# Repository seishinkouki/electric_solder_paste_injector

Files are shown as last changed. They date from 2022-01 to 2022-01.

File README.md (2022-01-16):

# electric_solder_paste_injector
## 电动锡膏注射器说明
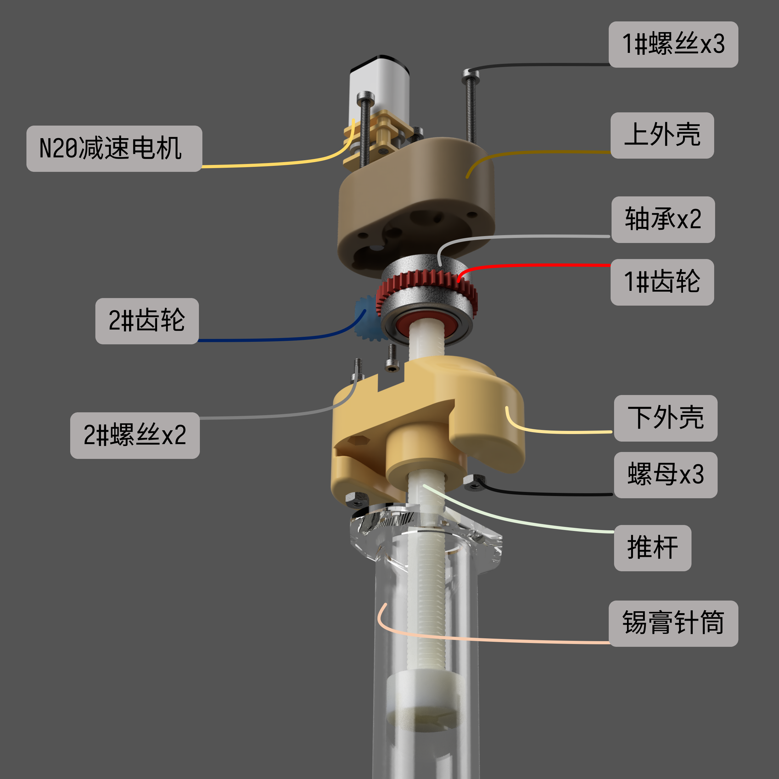
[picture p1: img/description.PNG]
图片

1. N20 减速电机: 5v电压, 150转左右均可, 出轴为10mm长, 直径3mm D轴, [淘宝链接](https://item.taobao.com/item.htm?id=592127519086)
2. 1#螺丝: m2x25mm, 淘宝购买
3. 2#螺丝: m1.6x4mm, 淘宝购买
4. 螺母: m2, 淘宝购买
5. 轴承: 内径12 外径18 厚4mm, 型号6701ZZ, [淘宝链接](https://detail.tmall.com/item.htm?id=585453925523&skuId=3967291013296)
6. 上外壳: 3d打印
7. 下外壳: 3d打印
8. 1#齿轮: 0.5模38齿, 3d打印
9. 2#齿轮: 0.5模15齿, 3mm D轴, [淘宝链接](https://item.taobao.com/item.htm?id=624015580884)
10. 推杆: 3d打印
11. 钢珠x6: 直径2mm, [淘宝链接](https://detail.tmall.com/item.htm?id=624796630554&skuId=4595617071063)
12. 锡膏针筒: 商品锡膏针筒
# 备注: 3d打印需使用尼龙材料才能达到强度要求, 已验证未来工场"尼龙加纤"材料, 其它尼龙材料理论也可行

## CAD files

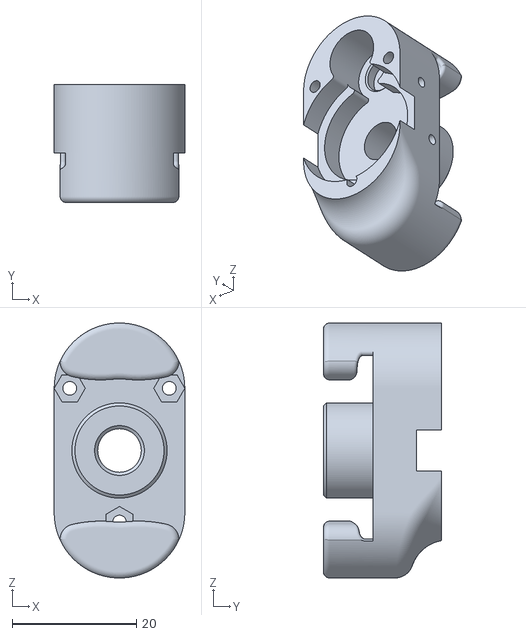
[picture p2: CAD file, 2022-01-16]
3d_model/下外壳.stl
21.0 x 19.0 x 41.0

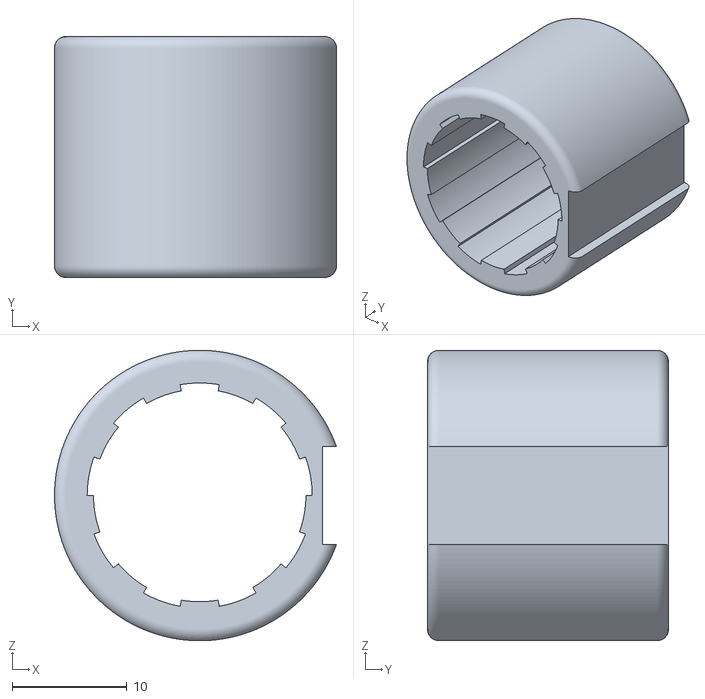
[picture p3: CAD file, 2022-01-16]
3d_model/控制.stl
24.6 x 21.0 x 25.3

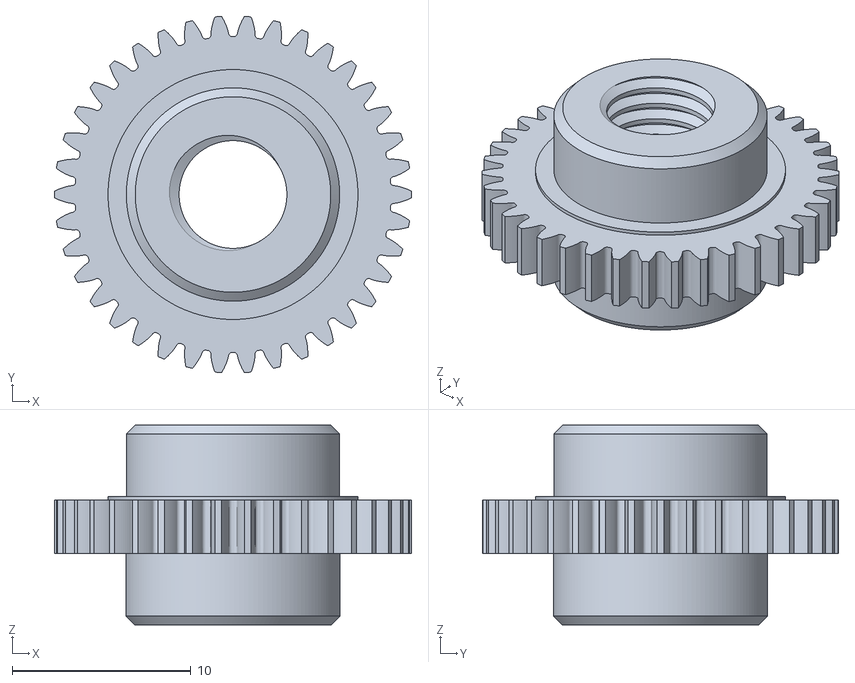
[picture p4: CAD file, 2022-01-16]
3d_model/齿轮.stl
20.0 x 20.0 x 11.2

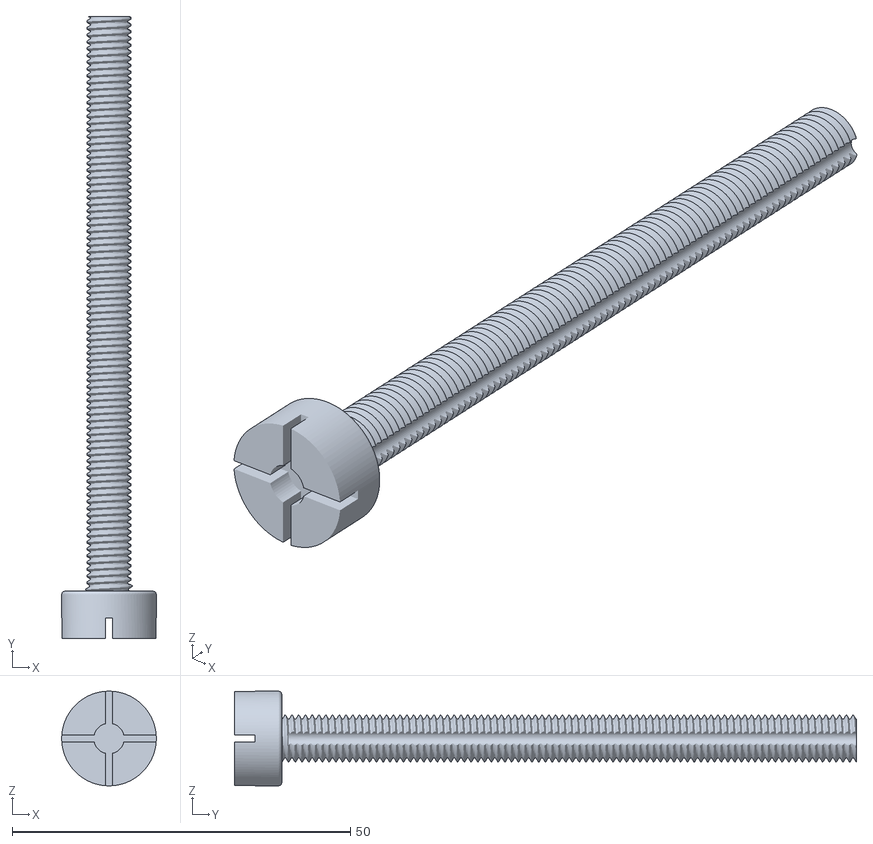
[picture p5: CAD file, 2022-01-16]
3d_model/推杆.stl
14.0 x 92.0 x 14.0

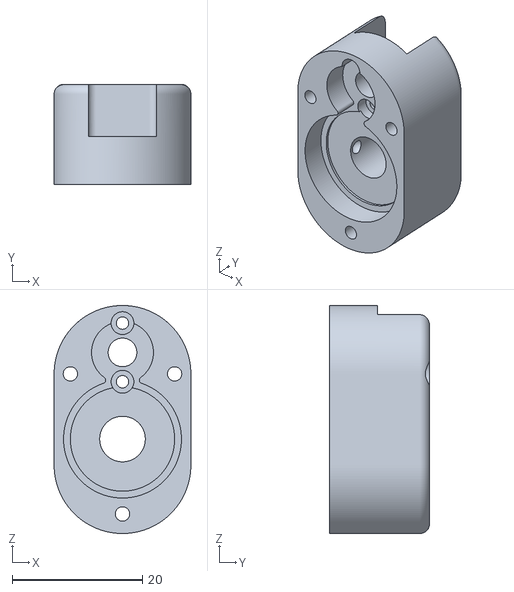
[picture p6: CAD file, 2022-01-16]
3d_model/上外壳.stl
21.0 x 15.4 x 35.0

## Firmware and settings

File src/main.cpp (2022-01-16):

#include <Arduino.h>
#include <AsyncTCP.h>
#include <Preferences.h>
#include <ESPAsyncWebServer.h>
#include <SPIFFS.h>
#include <Button2.h>

#define BUTTON_A_PIN  14
#define BUTTON_B_PIN  13
#define BUTTON_C_PIN  15
#define drv_sleep  18

bool motor_start = false;
bool fast_move_run = false;
bool fast_move_stop = false;
bool motor_back_run = false;
bool motor_back_stop = false;

Button2 buttonA, buttonB, buttonC;
AsyncWebServer server(80);
Preferences preferences;

const char* ssid = "OpenInjector";
const char* password = "123456789";

const char* PARAM_INPUT_1 = "input1";
const char* PARAM_INPUT_2 = "input2";
const char* PARAM_INPUT_3 = "input3";

unsigned int compresstime;
unsigned int maintaintime;
unsigned int pumpbacktime;

void notFound(AsyncWebServerRequest *request) {
  request->send(404, "text/plain", "Not found");
}

void motorloop() {
  if (motor_start) {
    ledcWrite(0, 0);
    ledcWrite(1, 1010);
    delay(compresstime);
    ledcWrite(0, 0);
    ledcWrite(1, 0);
    delay(maintaintime);
    ledcWrite(0, 1010);
    ledcWrite(1, 0);
    delay(pumpbacktime);
    ledcWrite(0, 0);
    ledcWrite(1, 0);
    motor_start = 0;
  }
  if (fast_move_run) {
    ledcWrite(0, 0);
    ledcWrite(1, 1010);
    fast_move_run = !fast_move_run;
  }
   if (fast_move_stop) {
    ledcWrite(0, 0);
    ledcWrite(1, 0);
    fast_move_stop = !fast_move_stop;
  }

  if (motor_back_run) {
    ledcWrite(1, 0);
    ledcWrite(0, 1010);
    motor_back_run = !motor_back_run;
  }
  if (motor_back_stop) {
    ledcWrite(1, 0);
    ledcWrite(0, 0);
    motor_back_stop = !motor_back_stop;
  }
}
void entersetuppage() {
  WiFi.softAP(ssid, password);

  server.on("/", HTTP_GET, [](AsyncWebServerRequest * request) {
    request->send(SPIFFS, "/index.html", "text/html");
  });
  server.on("/index.css", HTTP_GET, [](AsyncWebServerRequest * request) {
    request->send(SPIFFS, "/index.css", "text/css");
  });
  server.on("/script.js", HTTP_GET, [](AsyncWebServerRequest * request) {
    request->send(SPIFFS, "/script.js", "text/plain");
  });
  server.on("/getpara", HTTP_GET, [](AsyncWebServerRequest * request) {
    request->send(200, "text/plain", String(compresstime) + "," + String(maintaintime) + "," + String(pumpbacktime));
  });

  server.on("/leave.html", HTTP_GET, [](AsyncWebServerRequest * request) {
    server.end();
    preferences.putUInt("compresstime", compresstime);
    preferences.putUInt("maintaintime", maintaintime);
    preferences.putUInt("pumpbacktime", pumpbacktime);

    WiFi.mode(WIFI_OFF);
    btStop();
  });
  server.on("/leavewithoutsave.html", HTTP_GET, [](AsyncWebServerRequest * request) {
    server.end();
    WiFi.mode(WIFI_OFF);
    btStop();
  });


  server.on("/get", HTTP_GET, [] (AsyncWebServerRequest * request) {
    String inputMessage;
    if (request->hasParam(PARAM_INPUT_1)) {
      inputMessage = request->getParam(PARAM_INPUT_1)->value();
      compresstime = inputMessage.toInt();
    }
    else if (request->hasParam(PARAM_INPUT_2)) {
      inputMessage = request->getParam(PARAM_INPUT_2)->value();
      maintaintime = inputMessage.toInt();
    }
    else if (request->hasParam(PARAM_INPUT_3)) {
      inputMessage = request->getParam(PARAM_INPUT_3)->value();
      pumpbacktime = inputMessage.toInt();
    }
    else {
      inputMessage = "No message sent";
    }
    request->send(SPIFFS, "/index.html", "text/html");
  });
  server.onNotFound(notFound);
  server.begin();
}
void handler(Button2& btn) {
  if (btn == buttonA) {
    if (btn.getClickType() == LONG_CLICK) {
      entersetuppage();
    }
    else {
      motor_start = 1;
    }
  }
  else if (btn == buttonB) {
      Serial.println("B clicked");
    }
  else if (btn == buttonC) {
      Serial.println("C clicked");
  }
}
void pressedhandler(Button2& btn) {
  if (btn == buttonB) {
    Serial.println("B pressed");
    fast_move_run = true;
  }
  else if (btn == buttonC) {
    Serial.println("C pressed");
    motor_back_run = true;
  }
}
void releasedhandler(Button2& btn) {
  if (btn == buttonB) {
    Serial.println("B released");
    fast_move_stop = true;
  }
  else if (btn == buttonC) {
    Serial.println("C released");
    motor_back_stop = true;
  }
}
void doubleclickhandler(Button2& btn) {
if (btn == buttonC) {
    Serial.println("C double clicked");
    entersetuppage();
  }
}
void setup() {
  Serial.begin(115200);
  WiFi.softAP(ssid, password);

  if (!SPIFFS.begin()) {
    Serial.println("An Error has occurred while mounting SPIFFS");
    return;
  }
  preferences.begin("OpenInjector", false);
  compresstime = preferences.getUInt("compresstime", 300);
  maintaintime = preferences.getUInt("maintaintime", 100);
  pumpbacktime = preferences.getUInt("pumpbacktime", 200);

  buttonA.begin(BUTTON_A_PIN);
  buttonA.setDebounceTime(100);
  buttonA.setClickHandler(handler);
  // buttonA.setLongClickHandler(handler);

  buttonB.begin(BUTTON_B_PIN);
  buttonB.setDebounceTime(100);
  buttonB.setClickHandler(handler);
  buttonB.setPressedHandler(pressedhandler);
  buttonB.setReleasedHandler(releasedhandler);

  buttonC.begin(BUTTON_C_PIN);
  buttonC.setDebounceTime(100);
  buttonC.setClickHandler(handler);
  buttonC.setPressedHandler(pressedhandler);
  buttonC.setReleasedHandler(releasedhandler);
  buttonC.setDoubleClickHandler(doubleclickhandler);


  pinMode(drv_sleep, OUTPUT);
  digitalWrite(drv_sleep, LOW);

  ledcSetup(0, 1000, 10);
  ledcSetup(1, 1000, 10);
  ledcAttachPin(23, 0);
  ledcAttachPin(19, 1);
  ledcWrite(0, 0);
  ledcWrite(1, 0);
  digitalWrite(drv_sleep, HIGH);
  WiFi.mode(WIFI_OFF);
}

void loop() {
  buttonA.loop();
  buttonB.loop();
  buttonC.loop();
  motorloop();
}

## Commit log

2022-01-16 代码提交
2022-01-16 增加模型和硬件
    [上外壳.stl, 下外壳.stl, 控制.stl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]
2022-01-16 添加pcb gerber及bom
